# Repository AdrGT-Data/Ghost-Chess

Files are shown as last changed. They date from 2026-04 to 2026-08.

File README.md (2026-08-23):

# Ghost Chess: Data-Driven Hardware Project




> [!NOTE]
> Esto es un proyecto autodidacta que integra ingeniería de hardware, inteligencia artificial, análisis de datos y mecánica. 
> Se encuentra en desarrollo y es posible encontrar fallos tanto en código como en redacción o materiales.

## Objetivos y descripción del proyecto:

La **idea principal** del proyecto es crear un tablero físico de ajedrez que mueva las piezas mediante un electroimán situado en la parte inferior movilizado con un sistema CoreXY (como el de las impresoras 3D). Este tablero analizará los movimientos del jugador y responderá usando la inteligencia artificial **StockFish**, una IA entrenada y especializada en ajedrez. 

Además, como pasos a futuro, se guardarán los datos y jugadas de la partida con el fin de poder asesorar al jugador y ofrecer diversos servicios. Como último paso se realizará un modelo de predicción para prevenir el sobrecalentamiento térmico del imán.

## Stack Tecnológico
- **SO:** Linux (Ubuntu/Zorin)
- **Lenguaje:** Python 3.12 - C++
- **IA:** Stockfish Engine + Modelo predicción de sobrecalentamiento térmico
- **Hardware:** Arduino (CoreXY System)
- **Data: (Posibles cambios futuros):** SQLite / Streamlit 

<details>
<summary>Stockfish</summary>

Stockfish es un motor de ajedrez UCI (Interfaz de Ajedrez Universal) de código abierto para múltiples plataformas desarrollado por Tord Romstad, Joona Kiiski, Marco Costalba y Gary Linscott, con la colaboración de la comunidad de desarrolladores de código abierto. Se publica bajo la licencia GPLv3. Desde el 31 de mayo de 2014 la versión 5 está disponible en C++ y también precompilada para Windows, Linux, Mac y Android. Además está disponible una aplicación especial para iOS que funciona en iPhone, iPod touch y iPad.

Al igual que los motores mencionados, Stockfish soporta paralelismo y es compatible con sistemas operativos de 32 bits y 64 bits. También puede jugar el ajedrez aleatorio de Fischer.
</details>

## Estructura de Directorios
- `src/`: Lógica principal(python), hardware e IA y datos.
- `notebooks/`: Prototipado y experimentación.
- `data_raw/`: Logs de partidas y telemetría.
- `test/`: Archivos de prueba y experimentación.
- `Printables/`: Archivos `stl` para impresora 3D

## Estado del proyecto
- [x] Configuración de entorno Linux y venv.
- [x] Estructura de directorios.
- [x] Fase 0: Familiarización con librería `chess y lógica de IA (StockFish).
- [x] Fase 1: Simulación de partidas y tranformación de movimientos a coordenadas del tablero. 
- [x] Fase 2: Integración Hardware a la lógica del tablero.
- [x] Fase 3: Control de Precisión (Motores paso a paso).
- [ ] Fase 4: Montaje Mecánico CoreXY.
- [ ] Fase 5: Integración del ElectroImán.
- [x] Fase 6: Capa de Datos y Telemetría.
- [ ] Fase 7: Modelo de predicción de sobrecalentamiento térmico.

## FASE 1: Lógica de IA y Planificación de Movimientos

En esta etapa se desarrolla el "cerebro" del sistema, permitiendo que la lógica del juego se traduzca en coordenadas físicas precisas para el futuro sistema mecánico.

### Requerimientos:
- Python 3.12 o superior
- Archivo `chess_engine.py`

### Hitos Técnicos:
* **Integración de Motor de IA:** Implementación de **Stockfish 16** mediante la librería `python-chess` para el análisis de posiciones y toma de decisiones en tiempo real.
* **Sistema de Coordenadas Físicas:** Desarrollo de un traductor de notación algebraica (ej. `e2e4`) a milímetros reales. El sistema está optimizado para un tablero de **400x400 mm** con casillas de **50 mm**.
* **Algoritmo de Evasión de Colisiones (Pathfinding):** Implementación de una lógica de rutas que evita el choque entre piezas físicas. El imán se desplaza por los "pasillos" divisorios de las casillas, garantizando la integridad del juego.
* **Gestión del cementerio:** Implementación de un sistema que saca las piezas eliminadas del tablero.
* **Optimización de Seguridad:** Se ha definido un margen de seguridad basado en el diámetro de las piezas (**24 mm**) frente al tamaño de la casilla (**50 mm**), minimizando errores por fricción o interferencia magnética.

### Resultados:
Se ha logrado simular partidas completas en el terminal donde el sistema no solo decide la mejor jugada, sino que genera una lista de puntos $(x, y)$ que el hardware deberá recorrer.

## FASE 1.5: Creación de simulación de movimiento de imán al realizar los movimientos

### Requerimientos 

- Archivo `simulation.py`

Para ayudar a la visualización de los movimientos del iman al mover las piezas he creado un script `simulation.py` que mediante una representación gráfica del tablero se puede ver que movimientos realiza el imán en cada turno. Esto permite comprobar que no haya colisiones y que todo funcione correctamente.

## FASE 2: Integración Hardware

Una vez tenemos el código que nos da las coordenadas del tablero y los pasos para llegar a ellas, necesitamos una conexión que permita integrar la lógica de python con el hardware de Arduino.

Para lograr este hito he usado la comunicación bidireccional entre el sistema operativo Linux y el hardware de control mediante Python. En resumen, Arduino se queda continuamente esperando una señal concreta que python solo manda cuando el usuario se lo dice.

### Requerimientos
* `communication.py`
* Linux instalado
* Libreria `pyserial`
* Arduino R3
* Driver L298N
* Diodo LED
* Motores DC
* Pilas y portapilas

### Hitos Técnicos:

1.  **Test del LED (Señalización):**
    * Objetivo: Validar el protocolo de comunicación Serial y los permisos de puerto en Linux.
    * Resultado: Control de un diodo LED mediante envío de bytes (`1`/`0`) desde el terminal.
2.  **Control de Potencia (Tracción):** * Implementación de un puente en H **L298N** para gestionar la carga de motores DC.
    * Sincronización de tierras (GND) entre la fuente de potencia (pilas 18650) y la lógica de control (Arduino).
    * Resultado: Control direccional de motores desde Python.

Durante la implementación del sistema de agarre, se realizaron pruebas de estrés con el electroimán de 24V, obteniendo las siguientes conclusiones técnicas:

1. **Iteración del Control de Potencia**: Inicialmente se planteó el uso de un módulo **Relé** (Normalmente Abierto). Sin embargo, la carga inductiva del imán generaba caídas de tensión que provocaban el reinicio del microcontrolador Arduino por protección.
 
2. **Transición al Driver L298N**: Se optó por sustituir el relé por un módulo **L298N**. Esta configuración permite que los diodos de protección internos del driver absorban los picos de tensión al conmutar la carga, garantizando la estabilidad del sistema lógico y permitiendo el control mediante comandos seriales (`1` / `0`).
   
3. **Análisis de Eficiencia Energética**: Se detectó una deficiencia en la fuerza de atracción al alimentar el sistema con un pack de celdas Li-ion en serie (~14.8V - 16.8V).
   - **Fundamento Físico**: Considerando que la potencia disipada es proporcional al cuadrado del voltaje ($P = V^2 / R$), el funcionamiento a ~15V implica que el dispositivo opera apenas al **40% de su capacidad**.
   - **Resultado**: La densidad del campo magnético resultante es insuficiente para atravesar el tablero y desplazar las piezas con fiabilidad.

**Solución Prevista**: Usar un modulo elevador XL6019 que eleva la tensión y permite que imán funcione en su totalidad.

(Imagenes del circuito en la carpeta `docs`)

## FASE 2.5: Arquitectura CNC y Gestión Profesional (uv)

En esta etapa se ha realizado un "refactor" completo del sistema para pasar de un script de simulación a un software de control de maquinaria industrial (CNC).

### Hitos Técnicos:
* **Gestión con `uv`:** Migración del entorno a **uv**, garantizando una gestión de dependencias 100x más rápida y un entorno determinista mediante `pyproject.toml` y `uv.lock`.
* **Arquitectura Modular:** Separación de responsabilidades en tres núcleos:
    * `chess_engine.py`: Motor lógico y cálculo de trayectorias.
    * `communication.py`: Protocolo de comunicación Serial y sincronización de estados.
    * `main.py`: Orquestador de la aplicación.
* **Protocolo G-Code:** Implementación del estándar industrial para el control de movimiento. El sistema ahora genera instrucciones `G0` (tránsito rápido) y `G1` (movimiento de carga) que cualquier controlador CNC podría interpretar.
* **Lógica de Captura Inteligente:** Desarrollo de una coreografía de movimiento para capturas. El sistema detecta si la casilla destino está ocupada y genera automáticamente una fase de "eliminación", retirando la pieza capturada al cementerio antes de realizar el movimiento principal.

## FASE 3: Control de Precisión (Motores Nema17 paso a paso)

Hemos finalizado la integración del sistema nervioso del proyecto. Los motores responden correctamente a las órdenes de movimiento.

### Requerimientos

- Arduino R3
- CNC Shield
- 2 Drivers
- 2 Motores NEMA17
- Elevador de tensión
- Pilas y portapilas
- Universal Gcode Sender(UGS instalado)
- Electroimán

### Hitos Logrados:

- **Firmware:** Instalación y configuración de GRBL v1.1h.
- **Calibración:** Ajuste de voltaje de referencia a 0.6V para motores NEMA17.
- **Entorno:** Configuración de comunicación serial estable en Zorin OS (Linux).

### Especificaciones Técnicas

- **Motores:** 2x NEMA17.
- **Alimentación:** Pack 18650 (~15V) para motores y elevador de tensión XL6019 para electroimán (24V).
- **Software de control:** Universal Gcode Sender (UGS) y scripts personalizados en Python.

## FASE 4: Montaje Mecánico del CoreXY (Pausada)

Esta es la fase más tediosa de todas. Montaremos la estructura completa, usando como modelos los GIFs de la carpeta "docs". 

¿Qué vamos a hacer en esta sesión?

Ya tenemos todas las partes del proyecto, solo falta unirlas.

1. Montaje de la estructura mecánica CoreXY.
2. Instalación y tensado de correas GT2.
3. Pruebas de precisión y calibración de pasos por milímetro ($steps/mm$).
4. Integración del electroimán de 24V.

## FASE 6: Capa de Datos y Telemetría

>[!NOTE]
> Debido a la falta de material físico requerido para el montaje del tablero, se ha postpuesto la fase 4 y 5 para cuando sea posible adquirir los materiales.

En esta fase daremos rienda a nuestros conocimientos en bases de datos e intentaremos proporcionar un análisis de las partidas y con ello poder recrear partidas y ver diferentes datos de las partidas.

### Requerimientos

- Archivos `database.py`, `data_generator.py` y `ETL.py`

### Hitos logrados

- **Base de datos:** Se ha creado una base de datos en SQLite que se conecta con la partida ejecutada por `main.py` y que guarda los movimientos y el estado de las partidas.
- **Análisis de las partidas:** Se han simulado partidas creadas con la IA mediante el archivo `data_generator.py`.
- **Interfaz web Local:** Web local donde acceder a los datos de las partidas y poder reproducirlas.

## Fase 7: Modelo de prevención térmico (En proceso)

Como último paso nos centraremos en el mantenimiento a medio-largo plazo del mecanismo, centrandonos en el sobrecalentamiento del imán. Como no disponemos de un medidor de temperatura del imán, aproximaremos el indice de temperatura usando física y matemáticas. La idea es que un modelo ARIMA prediga la temperatura del imán en los próximos 3-5 turnos y lo apague o salte un aviso antes de llegar a una temperatura peligrosa.

### Requerimientos

- Archivo `database.py`

### Hitos conseguidos

- **Creacion de función térmica:** Se ha desarrollado una funcion que calcula el indice térmico en funcion de la temperatura anterior por fórmula física.

*Continuará*

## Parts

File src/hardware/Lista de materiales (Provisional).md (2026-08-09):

# Lista de materiales (Provisional)

Aquí se muestra el itinerario donde muestro todos los materiales que he ido usando durante el proyecto. 

> [!WARNING]
> Se advierte que esta lista puede ir cambiando con el progreso del proyecto.

## Hardware

- 4 Pilas 18650 de Litio de 3.7V y sus respectivos portapilas
- Cable de cobre 
- Resistencias de 220, 1k y 10k.
- Diodos led para pruebas
- Motores DC (Opcional)
- Arduino UNO
- Modulo L298N
- Electroimán 24V de 2,5 cm de diámetro
- 2 modulos A4988
- Placa expansión Arduino CNC Shield V3
- 2 Motores NEMA17
- Modulo elevador XL6019
- Modulo pantalla táctil ESP32-S3 con altavoz y micrófono

## Montaje

- 4 piezas de rodamiento Lineal LM8UU
- Correa de 2 metros y 6 poleas dentadas
- 4 varillas de acero 8mm
- Placa de madera
- Tornillos de madera 4x30
- Piezas impresas en 3D

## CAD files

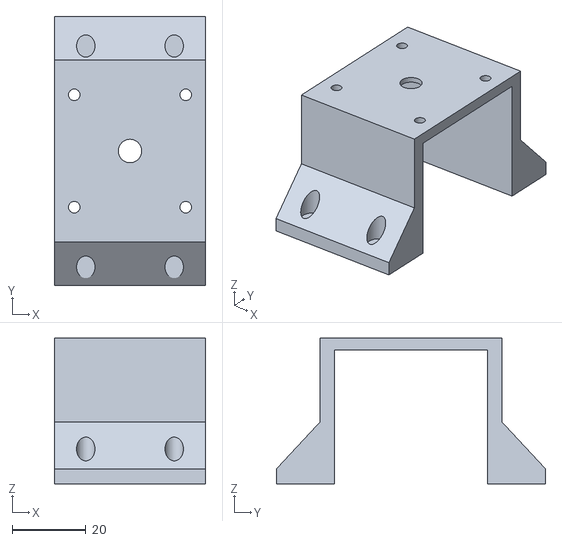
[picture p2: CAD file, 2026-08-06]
Printables/NEMA17 mount.stl
41.0 x 73.0 x 39.5

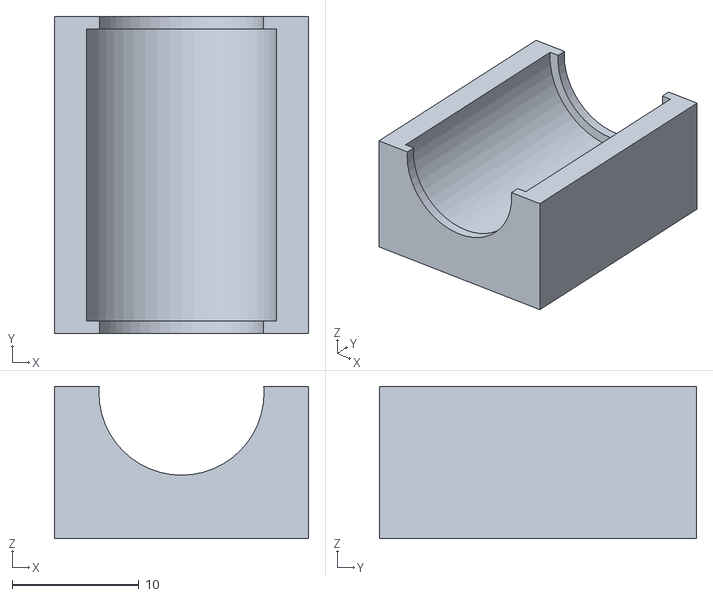
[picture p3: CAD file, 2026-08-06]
Printables/Soporte Rodamiento.stl
20.0 x 25.0 x 12.0

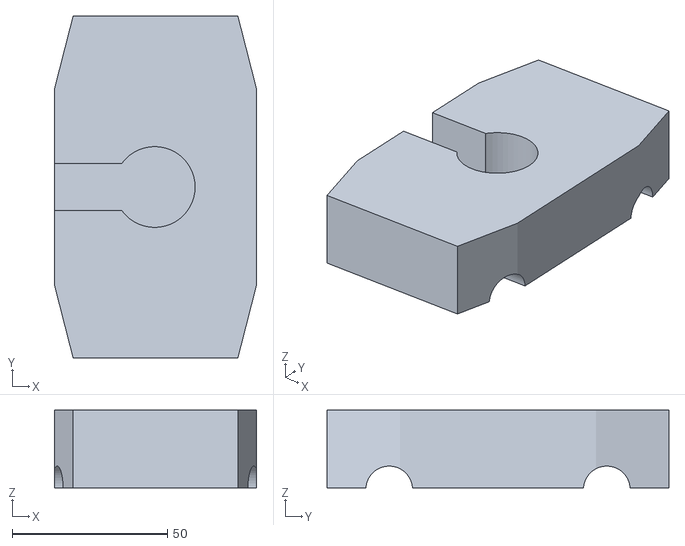
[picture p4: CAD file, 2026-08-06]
Printables/Base iman.stl
65.0 x 110.0 x 25.0

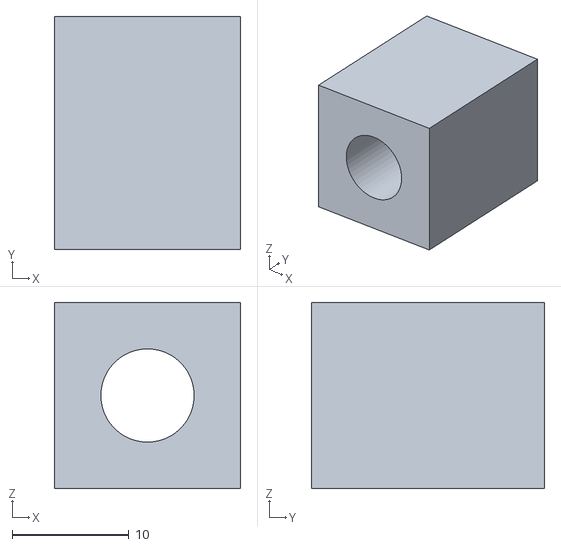
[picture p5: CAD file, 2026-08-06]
Printables/Soporte varillas.stl
16.0 x 20.0 x 16.0

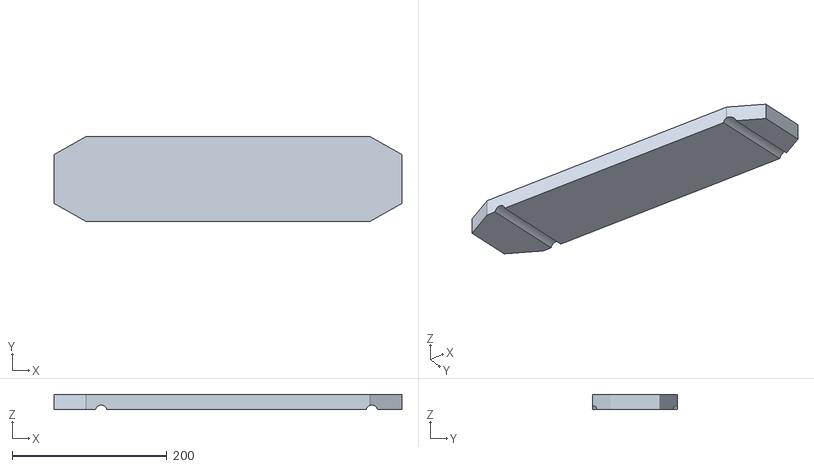
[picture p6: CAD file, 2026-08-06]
Printables/Base Ajedrez.stl
450.0 x 110.0 x 20.0

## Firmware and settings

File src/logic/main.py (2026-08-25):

from chess_engine import GhostChessEngine
from communication import SerialComunicator
from simulation import MagnetSimulator 
from database import DatabaseManager
import chess
import time

def main():
    # 1. SETUP
    sim = MagnetSimulator()

    game = GhostChessEngine(difficulty=1)

    #Incializamos la base de datos y creamos una nueva partida
    db = DatabaseManager()
    id_partida = db.iniciar_partida(dificultad_ia=5)
    turnos = 0

    sim.draw_pieces(game.board)
    #arduino = SerialComunicator(port='/dev/ttyUSB0', baudrate=115200) 

    while not game.board.is_game_over():

        # 2. ----------------------JUGADA IA-------------------------

        print(f"\n--- TURNO IA ---")

        #Disparamos el cronómetro
        inicio_calculo_ia = time.time()

        best_move = game.get_best_move()

        #Detenemos el cronómetro
        fin_calculo_ia = time.time()
        tiempo_calculo_ia_ms = (fin_calculo_ia - inicio_calculo_ia) * 1000  # Convertimos a milisegundos

        processed_gcode = game.process_full_move(best_move)

        game.play_move(best_move)

        # 2.1 Simulación visual del movimiento de la IA
        sim.simulate_gcode(processed_gcode)
        sim.draw_pieces(game.board)  # Actualizamos la visualización del tablero después del movimiento de la IA

        # 2.2 Registro de la jugada de la IA en la base de datos
        distancia_gcode_mm_ia = db.calcular_distancia_gcode(processed_gcode)
        db.registrar_turno(
            id_partida=id_partida,
            numero_turno=turnos,
            jugador="IA_Blancas",
            movimiento_uci=best_move.uci(), # Extraemos el texto
            estado_fen=game.board.fen(),    # Extraemos la foto FEN actual
            tiempo_calculo_ms=tiempo_calculo_ia_ms,# Usamos el tiempo calculado
            distancia_mm=distancia_gcode_mm_ia,      #Calculamos distancia recorrida por el imán en mm 
            tiempo_iman_ms=db.calcular_tiempo_iman(distancia_gcode_mm_ia), # Calculamos el tiempo que ha tardado el imán en recorrer la distancia
            indice_termico = db.calcular_indice_termico(id_partida, turnos)
        )
        turnos += 1

        # 3. ------------------------------JUGADA HUMANA------------------------------
        try:
            # Disparamos cronómetro para medir el tiempo de entrada del jugador
            inicio_entrada_humana = time.time()

            # Pedimos al jugador que introuzca su jugada en formato UCI (ej: e2e4)
            human_move_input = input("Introduce tu jugada (formato UCI, ej: e7e5): ")

            #Quitamos los espacios ineccesarios
            human_move_input = human_move_input.strip() 
            
            # Traducimos el texto a un objeto Move de python-chess
            human_move = chess.Move.from_uci(human_move_input)
                
            # Verificamos si es legal en el ESTADO ACTUAL del tablero
            if human_move in game.board.legal_moves:

                # Paramos el cronómetro para medir el tiempo de entrada del jugador
                fin_entrada_humana = time.time()
                tiempo_entrada_humana_ms = (fin_entrada_humana - inicio_entrada_humana) * 1000  # Convertimos a milisegundos

                #Movimiento humano válido, procesamos y simulamos
                gcode_human = game.process_full_move(human_move)
                sim.simulate_gcode(gcode_human)
                game.play_move(human_move)  # Actualizamos el estado con la jugada humana
                sim.draw_pieces(game.board)  # Actualizamos la visualización del tablero después de
                    
                # Registramos el turno humano en la base de datos
                distancia_gcode_mm_humano = db.calcular_distancia_gcode(gcode_human)
                db.registrar_turno(
                    id_partida=id_partida,
                    numero_turno=turnos,
                    jugador="Humano_Negras",
                    movimiento_uci=human_move.uci(), # Extraemos el texto
                    estado_fen=game.board.fen(),    # Extraemos la foto FEN actual
                    tiempo_calculo_ms=tiempo_entrada_humana_ms,          # Usamos el tiempo calculado
                    distancia_mm=distancia_gcode_mm_humano,         # Ignorado por hoy
                    tiempo_iman_ms=db.calcular_tiempo_iman(distancia_gcode_mm_humano),              # Ignorado por hoy
                    indice_termico = db.calcular_indice_termico(id_partida, turnos)
                )
                turnos += 1

            else:
                print("Movimiento invalido. Intenta de nuevo.")
                    
        except ValueError:
            # Atrapamos el error si el usuario escribe un formato que no es UCI (ej: "hola", "peon a4")
            print("Formato incorrecto. Introduce el formato UCI de origen y destino (ej: e7e5).")


    #gcode = game.process_full_move(best_move)

    # 3. Comunicación con Arduino (desactivada por ahora)
    #arduino.connect()
    #arduino.send_gcode(gcode)
    #arduino.disconnect()

    # CIERRE DE LA SIMULACIÓN Y DEL MOTOR
    db.cursor.execute("UPDATE Partidas SET resultado = 'Finalizada' WHERE id_partida = ?", (id_partida,))
    db.conn.commit()
    db.close()
    
    sim.screen.exitonclick()  # Cierra la ventana de simulación al hacer clic
    game.close()

if __name__ == "__main__":
    main()

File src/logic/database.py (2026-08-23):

import sqlite3
import os
import time
import math

"""
Este módulo contiene la clase DatabaseManager, que se encarga de gestionar la base de datos SQLite para almacenar la telemetría de las partidas de ajedrez simuladas.
La base de datos contiene dos tablas principales:
1. PARTIDAS: almacena información general de cada partida (fecha, dificultad, resultado).
2. TELEMETRIA_TURNOS: almacena información detallada de cada turno (jugador, movimiento, estado del tablero, tiempo de cálculo, distancia recorrida por el imán, tiempo que el imán estuvo encendido).
"""

class DatabaseManager:
    def __init__(self, db_name="ghost_chess_telemetry.db"):
        """
        Inicializa la conexión y asegura que el esquema exista.
        """
        # Creamos una carpeta data si no existe para mantener el proyecto limpio
        self.db_dir = os.path.join(os.path.dirname(os.path.abspath(__file__)), "..", "data")
        # Si la carpeta ya esta creada, no hacemos nada. Si no, la creamos.
        os.makedirs(self.db_dir, exist_ok=True)

        # Definimos la ruta completa de la base de datos
        self.db_path = os.path.join(self.db_dir, db_name)
        # Conectamos a la base de datos (se crea si no existe)
        self.conn = sqlite3.connect(self.db_path)
        # Creamos un cursor para ejecutar comandos SQL
        self.cursor = self.conn.cursor()
        
        self._create_tables()

    def _create_tables(self):
        """
        Crea las tablas relacionales.
        """

        # Entidad Partidas: almacena información general de cada partida
        # Entidad Telemetria_Turnos: almacena información detallada de cada turno
        self.cursor.execute('''
            CREATE TABLE IF NOT EXISTS PARTIDAS (
                id_partida INTEGER PRIMARY KEY AUTOINCREMENT,
                fecha_inicio DATETIME DEFAULT CURRENT_TIMESTAMP,
                dificultad_ia INTEGER,
                resultado TEXT DEFAULT 'En curso'
            )
        ''')

        self.cursor.execute('''
            CREATE TABLE IF NOT EXISTS TELEMETRIA_TURNOS (
                id_turno INTEGER PRIMARY KEY AUTOINCREMENT,
                id_partida INTEGER,
                numero_turno INTEGER,
                jugador TEXT,
                movimiento_uci TEXT,
                estado_fen TEXT,
                tiempo_calculo_ms REAL,
                distancia_mm REAL,
                tiempo_iman_ms REAL,
                indice_termico REAL,
                FOREIGN KEY(id_partida) REFERENCES PARTIDAS(id_partida)
            )
        ''')

        # Guardamos los cambios y confirmamos que la base de datos está lista
        self.conn.commit()
        print(f"Base de datos operativa en: {self.db_path}")

    def iniciar_partida(self, dificultad_ia):
        """
        Crea una nueva fila en PARTIDAS al iniciar el programa.
        Retorna el id_partida autogenerado para usarlo en los turnos.
        """
        query = '''
            INSERT INTO PARTIDAS (dificultad_ia)
            VALUES (?)
        '''
        # Ejecutamos el insert pasando la dificultad como tupla
        self.cursor.execute(query, (dificultad_ia,))
        self.conn.commit()
        
        # Obtenemos el ID que SQLite acaba de autogenerar y lo retornamos para usarlo en los turnos
        id_partida_actual = self.cursor.lastrowid
        
        return id_partida_actual

    def registrar_turno(self, id_partida, numero_turno, jugador, movimiento_uci, 
                        estado_fen, tiempo_calculo_ms, distancia_mm, tiempo_iman_ms, indice_termico):
        """
        Inserta un evento en Telemetria_Turnos vinculado a la partida actual.
        """
        query = '''
            INSERT INTO Telemetria_Turnos (
                id_partida, numero_turno, jugador, movimiento_uci, 
                estado_fen, tiempo_calculo_ms, distancia_mm, tiempo_iman_ms, indice_termico
            )
            VALUES (?, ?, ?, ?, ?, ?, ?, ?, ?)
        '''
        valores = (id_partida, numero_turno, jugador, movimiento_uci, 
                   estado_fen, tiempo_calculo_ms, distancia_mm, tiempo_iman_ms, indice_termico)
        
        self.cursor.execute(query, valores)
        self.conn.commit()

    def calcular_distancia_gcode(self, gcode_list):
        """
        Calcula la distancia total en mm que recorrerá el robot según las instrucciones G-code.
        gcode_instructions: lista de strings con instrucciones G-code (ej: ["G1 X10 Y20", "G1 X15 Y25"])
        """
        total_distance = 0.0
        last_x, last_y = None, None

        for instruction in gcode_list:
            # Solo nos interesan las instrucciones de movimiento lineal (G0 y G1)
            if instruction.startswith("G0") or instruction.startswith("G1"):
                parts = instruction.split()
                x, y = None, None

                for part in parts:
                    if part.startswith("X"):
                        x = float(part[1:])
                    elif part.startswith("Y"):
                        y = float(part[1:])

                # SI tenemos coordenadas válidas, calculamos la distancia
                if x is not None and y is not None:
                    if last_x is not None and last_y is not None:
                        dx = x - last_x
                        dy = y - last_y
                        distance = math.sqrt(dx**2 + dy**2)
                        total_distance += distance
                    
                    last_x, last_y = x, y

        return total_distance

    def calcular_tiempo_iman(self, distancia_mm, velocidad_mm_s=50.0):
        """
        Calcula el tiempo estimado que tardará el imán en mover la pieza según la distancia.
        velocidad_mm_s: velocidad promedio del imán en mm/s (ajustable según pruebas)
        """
        if velocidad_mm_s <= 0:
            raise ValueError("La velocidad debe ser mayor que cero.")
        
        tiempo_segundos = distancia_mm / velocidad_mm_s
        return tiempo_segundos * 1000  # Convertimos a milisegundos

    def calcular_indice_termico(self, id_partida, numero_turno, temperatura_ambiente = 25, k_cool= 0.05, k_heat = 2.5):
        """
        Calcula un índice térmico simple basado en el tiempo que el imán estuvo encendido y el tiempo de cálculo de la IA.
        Este índice es una métrica inventada para evaluar la "carga térmica" del sistema.
        """

        # Recuperamos los datos del turno desde la base de datos
        tiempo_calculo_ms, tiempo_iman_ms = None, None
        self.cursor.execute("""
            SELECT tiempo_calculo_ms, tiempo_iman_ms 
            FROM Telemetria_Turnos 
            WHERE id_partida = ? AND numero_turno = ?
        """, (id_partida, numero_turno))

        actual_row = self.cursor.fetchone()
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

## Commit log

2026-01-20 Initial commit: Estructura de proyecto y entorno virtual
2026-01-21 Fase 0 completa: Lógica de StockFish, traducción a mm y pathfinding para evitar colisiones
2026-01-26 Añadidos scripts de prueba para comunicación Serial en carpeta test
2026-01-26 Guardando cambios locales del README antes de fusionar
2026-01-27 Magnet.py subido
2026-01-27 Magnet.ino subido
2026-01-27 Revise technical note for Phase 2 on electromagnet tests
    Updated technical note for Phase 2 with detailed analysis of the electromagnet and power control iterations.
2026-02-06 Cambio de uv
